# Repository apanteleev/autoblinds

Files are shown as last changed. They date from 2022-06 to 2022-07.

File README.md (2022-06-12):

# AutoBlinds

This repository contains various project files necessary to build a smart home connected device that moves a roller shade up and down by its bead string. The automation part is based on an ESP8266 microcontroller that talks to an automation hub via Wi-Fi and MQTT and is fully compatible with Home Assistant. The mechanical part is based on a NEMA 17 stepper motor with a TMC2208 driver, and the case and gears are 3D printed. Using a 48mm 2A stepper motor is sufficient to move a heavy 2.6 x 2.4 meter roller blind up or down in 20 seconds.

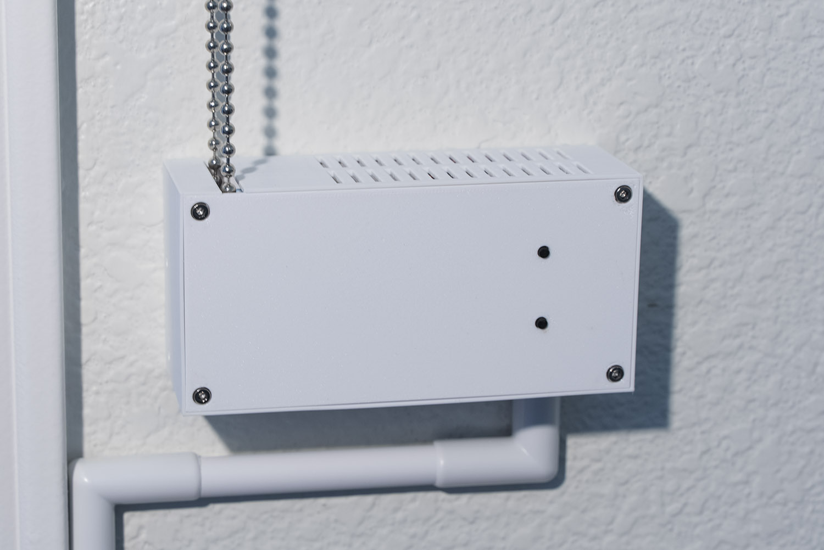
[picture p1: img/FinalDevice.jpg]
Final Device Image


## Origin

The project is inspired by another similar project, [ESPBlinds by se1exin](https://github.com/se1exin/ESPBlinds). The only parts reused from that project are the small gear and chain gears, everything else is rebuilt from scratch.

The main improvements are:

- Local control with up and down buttons
- Shade movement limits programmable from the buttons
- Soft start and stop
- Revised MQTT interface that is easily compatible with Home Assistant and supports moving the shade to a specific position
- Much smaller device by using a smaller big gear and packing things tighter in the case
- Quieter operation with the TMC2208 silent stepper driver

## Software

The software for the ESP8266 module is included here, see the [`autoblinds.ino`](autoblinds.ino) file. It builds with Arduino IDE version 1.8.19.

Additional steps before building:

- Install the ESP8266 boards for Arduino, see [this manual](https://arduino-esp8266.readthedocs.io/en/latest/installing.html)
- Install the PubSubClient library through the Arduino Library Manager.
- Copy the [`constants.example.h`](constants.example.h) file into `constants.h` and adjust the settings to match your network setup.

Build the project and program the board, it *should* work and report a connection to WiFi and MQTT through the serial port.

## Device Overview

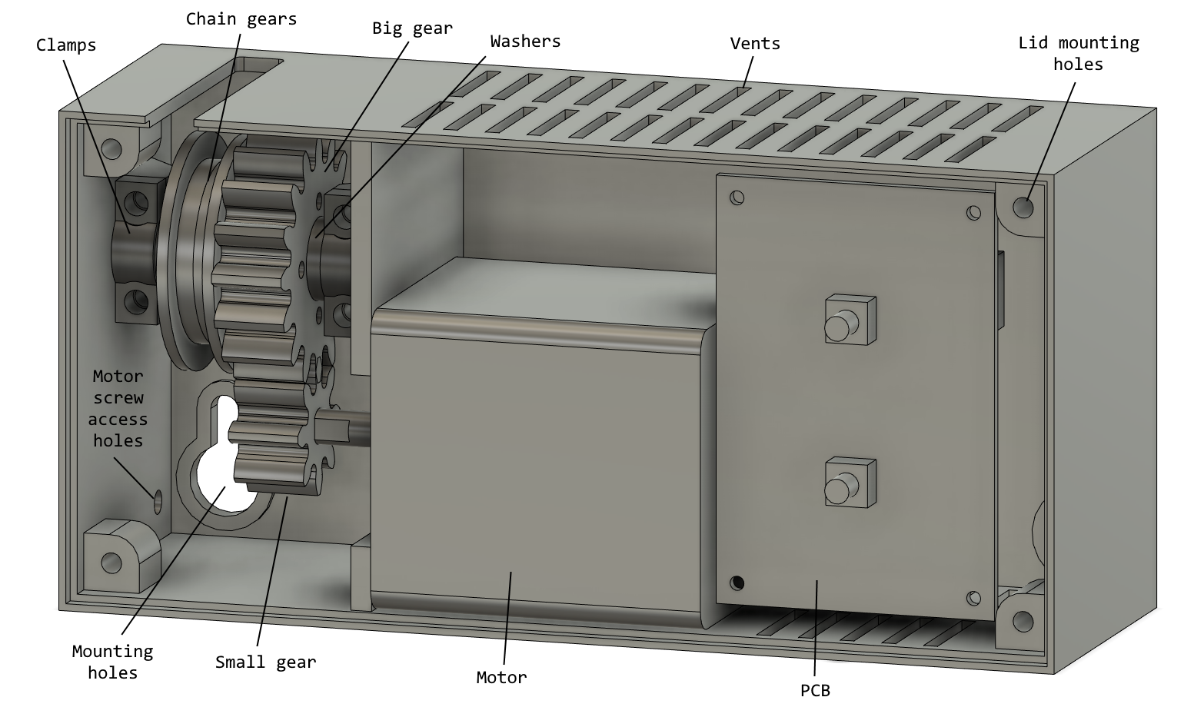
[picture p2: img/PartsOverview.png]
Parts Overview


## Button Operation

- Press the Up button to open the shade up to the top limit.
- Press the Down button to close the shade down to the bottom limit.
- While the shade is moving, press any button to stop it.
- Hold the Up button and press the Down button to set the top limit.
- Hold the Down button and press the Up button to set the bottom limit.
- Hold the Up or Down button for more than 0.5 seconds to open or close the shade beyond the limits (useful for setting the limits).

Note that while the limits are not set, the shade will not stop automatically. After assembling the device and uploading the program, make sure to set the limits first.

## Schematic Diagram

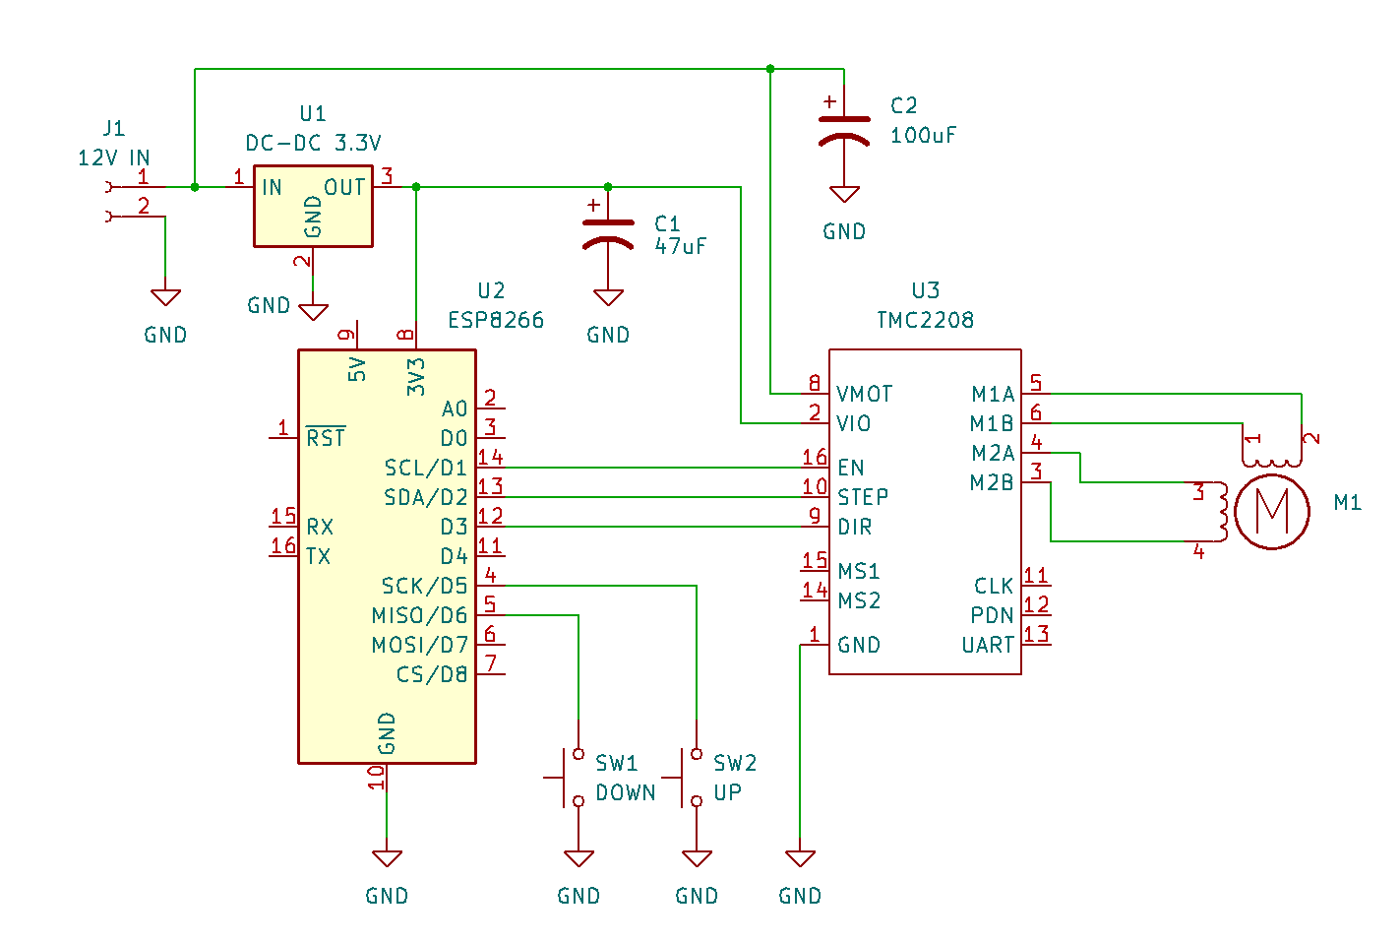
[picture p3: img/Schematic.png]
Schematic Diagram


## Parts

You'll need the following parts:

- 3D printed case and gears, including 2x ChainGear model. Use PETG filament for best results, not PLA. The models are available in the [models](models) folder in STL and as a Fusion 360 project.
- [ESP8266 board](https://www.amazon.com/dp/B081PX9YFV)
- [DC-DC converter](https://www.amazon.com/dp/B01MQGMOKI) capable of turning your input voltage into 3.3V for the ESP
- [TMC2208 stepper driver](https://www.amazon.com/dp/B08XV1HKYF)
- [NEMA 17 stepper motor](https://www.amazon.com/dp/B00PNEQKC0)
- 12-24V 2A+ power supply
- [4x6cm prototype PCB](https://www.amazon.com/dp/B07NM68FXK) and some header connectors
- [Push button switches](https://www.amazon.com/dp/B01MRP025V) - 2pc 6x6x8 mm
- Screws with hex caps: 12pc M3x8, 4pc M3x16, 4pc M2x6 - I used [this set](https://www.amazon.com/dp/B08JCKH31Q)
- Screws or anchors to mount the device to the wall - the selection depends on the wall material.
- Generic capacitors, wires, etc.
- Some grease and a Dremel with small drill bits

## Finished PCB

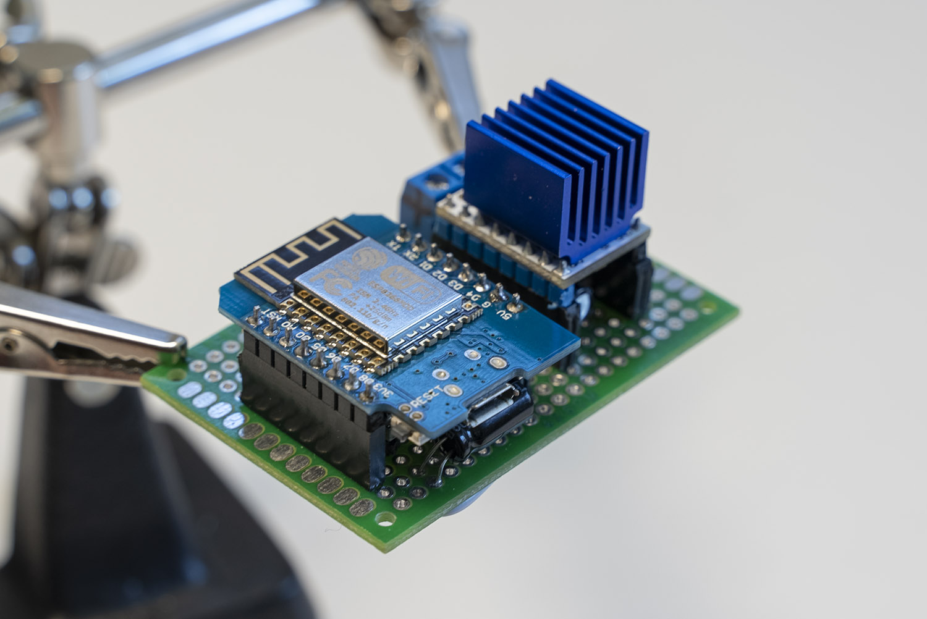
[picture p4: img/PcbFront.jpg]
Board Front Side


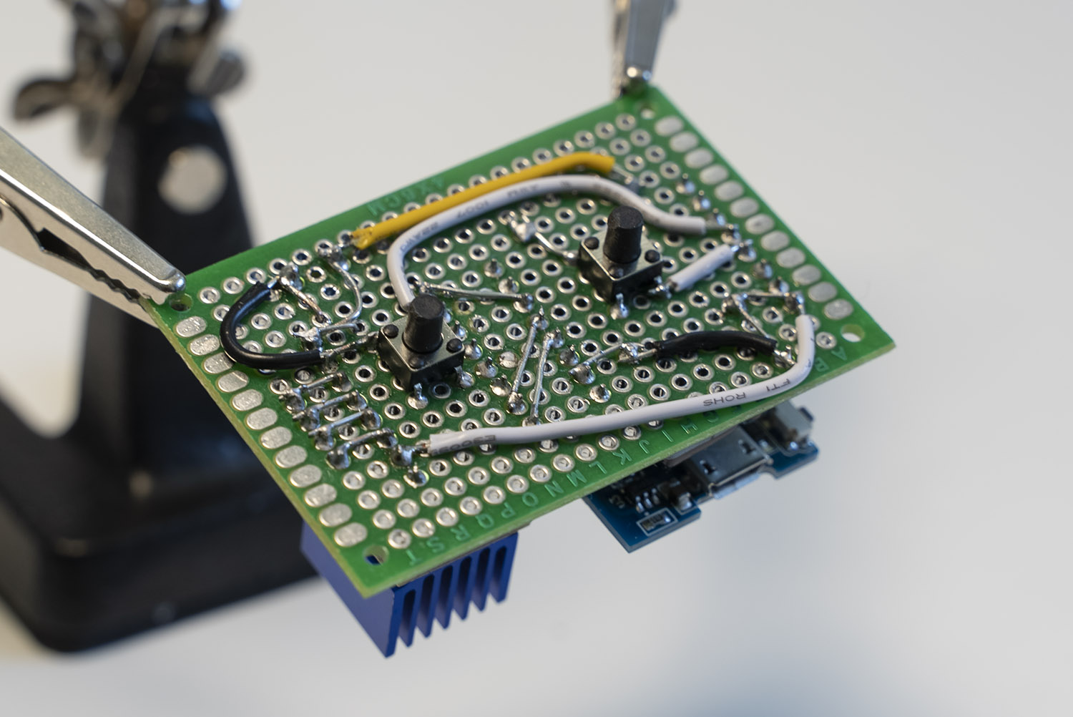
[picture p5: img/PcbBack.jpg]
Board Back Side


## Assembly steps

- Print the mechanical parts. None of them need any supports. The axle should be printed vertically with a brim, using as many perimeters as necessary to fill the entire volume.
- Drill the screw holes in the lid for the 4 M3 screws to pass freely.
- Put the small gear onto the motor axle. The fit should be very snug.
- Attach the motor to the case with 4 M3x8 screws. The two screws in the back can be accessed by putting an Allen key through the special holes on the left of the case.
- Connect the chain gears with the big gear using 4 M3x16 screws. The screws won't go easily through the holes in the chain gears, so just drill the holes a bit wider. I didn't design those chain gears so can't easily fix the models.
- Attach the PCB to the lid using 4 M2x6 screws.
- Put the big gear assembly onto the axle, add the washers - the wide one on the left, the narrow one on the right. The wide washer will need a little bit of Dremeling to fit between the screw heads.
- Make sure that the gear assembly and the axle fit into the case and things rotate freely. There might be some more Dremeling necessary to make things fit with little friction.
- Put the bead string through the chain gears.
- Insert the gear assembly into the case, secure the axle with the two clamps and tighten them with 4 M3x8 screws.
- Hold the device against the wall to figure out the right position to tension the string.
- Mount the device to the wall. Note that the mounting holes have vertical slots to adjust the tension. *In case you're wondering why the mounting holes are at the bottom, that's because when the device starts pulling on the string, this way it will just push the top side into the wall.*
- Connect the motor to the PCB, power it up and test.
- Adjust the current limiter on the stepper driver to make sure the current is enough to raise the shade without stalling. You may also want to adjust the speed parameters in the program, look for `MOTOR_MIN_SPEED`, `MOTOR_MAX_SPEED` and `MOTOR_ACCELERATION` in [`autoblinds.ino`](autoblinds.ino). Note that those steps are actually microsteps, and the default microstep for TMC2208 is 1/8 step when both MS1 and MS2 pins are low.
- Apply some grease on the gears and axle. This will likely require removing the gear assembly from the case, but doing it earlier would just be messy.
- Close the lid with 4 M3x8 screws. The lid may stick out in the middle; if that's the case, just put it on the 3D printer heatbed, heat that to the print temperature, and bend the lid a few degrees inwards. After cooling down, the lid will act like a spring.

## More Pictures

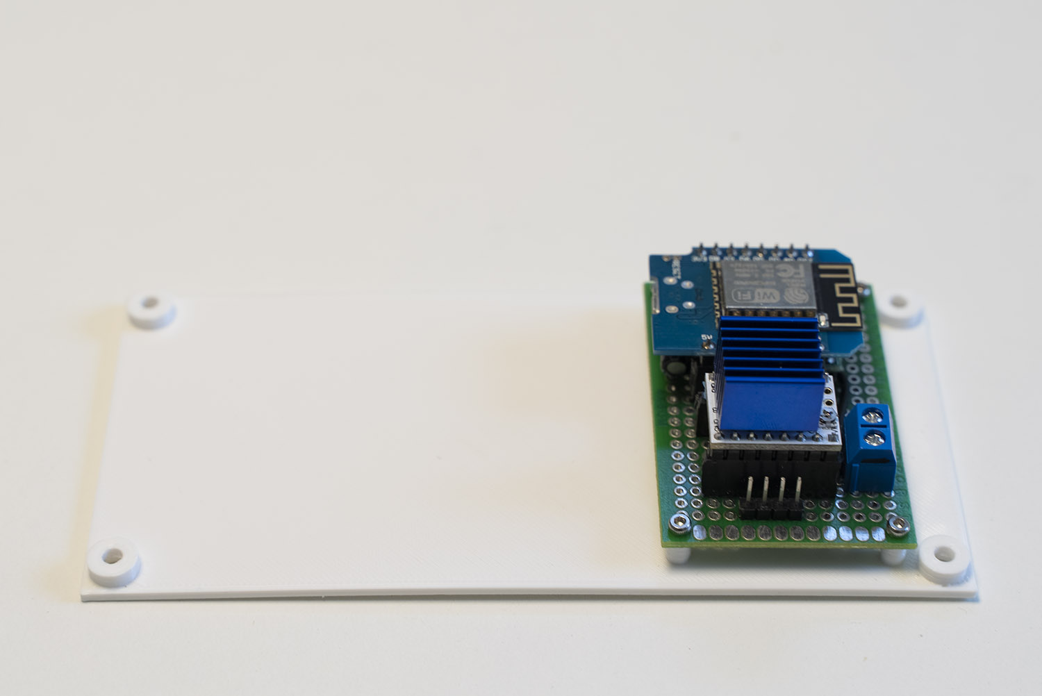
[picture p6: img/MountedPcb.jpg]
PCB Mounted on the Lid


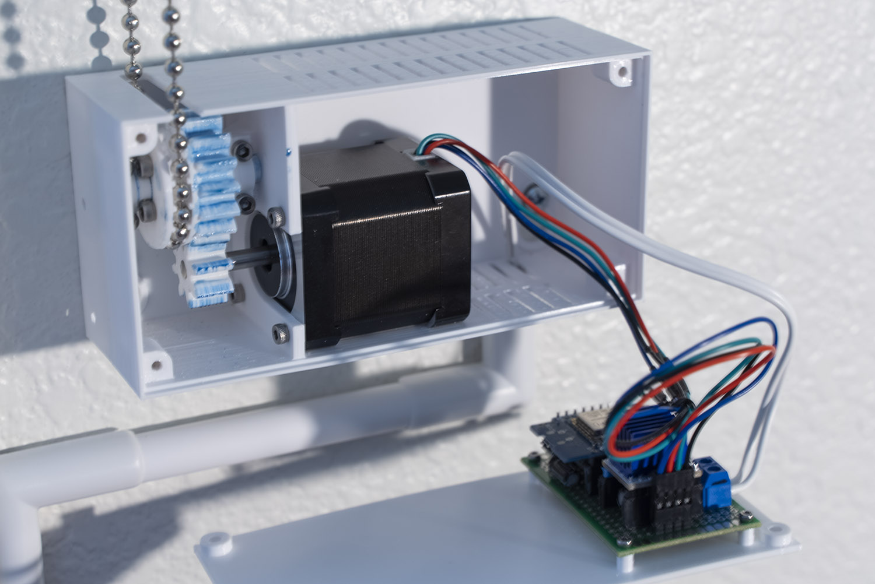
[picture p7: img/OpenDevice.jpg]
Assembled Device without Lid


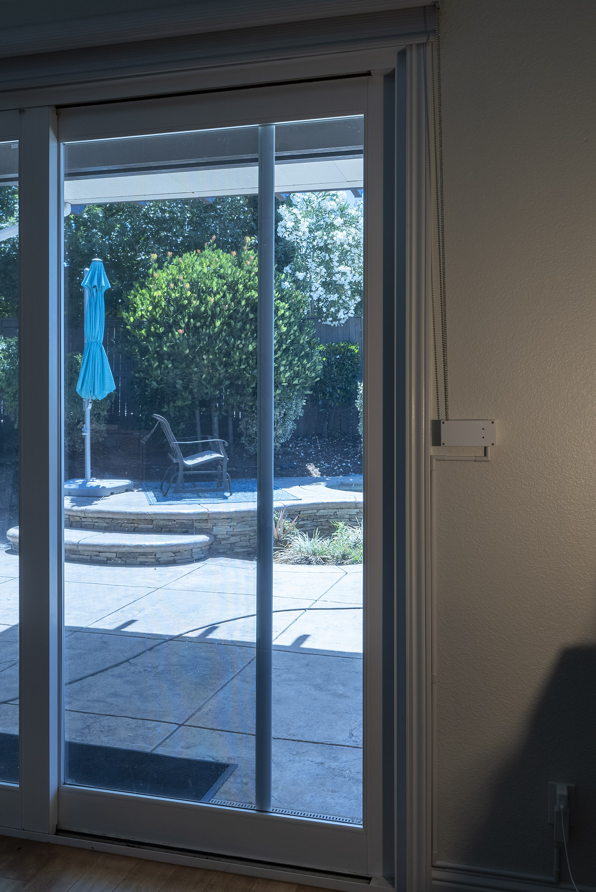
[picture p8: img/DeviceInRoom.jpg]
Device In The Room


## Home Assistant Integration

Home Assistant supports [MQTT shades](https://www.home-assistant.io/integrations/cover.mqtt) ("covers") natively, so you'll need to add something like this to `configuration.yaml`:

```yaml
mqtt:
  cover:
  - name: "Friendly Name"
    availability:
      # Note that the topic root used here 5 times (home/blinds/)
      # must match MQTT_TOPIC_ROOT defined in constants.h
      - topic: "home/blinds/status"
    command_topic: "home/blinds/command"
    payload_open: "open"
    payload_close: "close"
    payload_stop: "stop"
    position_topic: "home/blinds/position"
    set_position_topic: "home/blinds/setposition"
    state_topic: "home/blinds/state"
```

Obviously, you'll also need an [MQTT broker](https://mosquitto.org), but that's very easy to set up.

## What Could Be Improved

- Limit switches would solve the issue of position drift: when the motor disengages, the gears move a bit releasing the string tension. That movement is not registered by the controller. Also, if someone moves the shade manually, the limits currently need to be reset because manual motion is also not registered by the MCU.
- There's no user-friendly way of setting up the Wi-Fi and MQTT parameters. Other devices host an access point that is used for such initial setup.
- The orientation of the driver module makes the radiator fins horizontal, while vertical orientation is better. Originally I used the DRV8825 driver, and its radiator could be attached the other way.
- The orientation of the ESP module on my PCB prevents attaching a USB cable without removing the board from the device.
- No barrel connector for power, although it's not much of a problem as the cable just goes through one of the vent slots and into the cord cover.
- Tiny round buttons sticking out don't look so well, and it's possible to make button caps with e.g. triangular shape pointing up and down. The buttons should probably be shorter in that case, and the lid holes should match the button shape.
- Using a real custom PCB would just look better.

## Feedback

If you have any suggestions or comments, feel free to post issues or pull requests here on GitHub. Constructive criticism is welcome, especially considering that I'm relatively new to this type of engineering.

## License

This project is distributed under the terms of the [MIT License](LICENSE.txt).

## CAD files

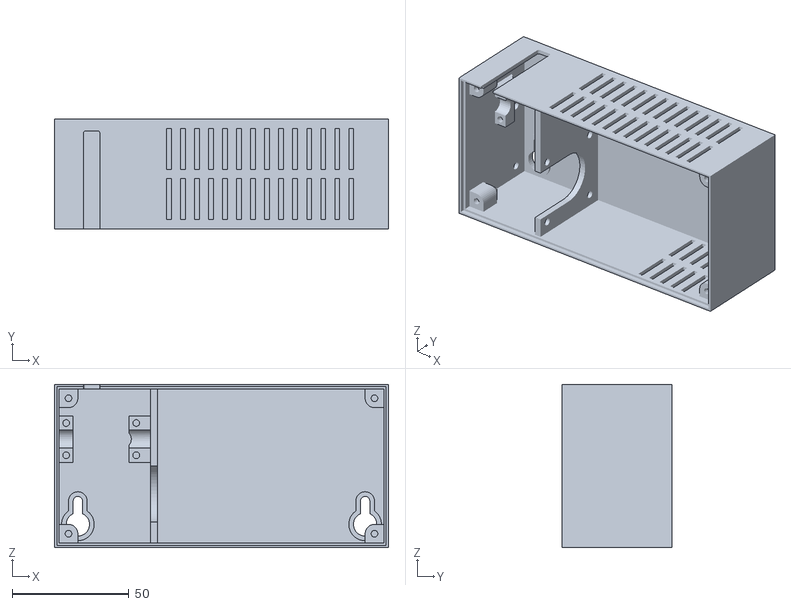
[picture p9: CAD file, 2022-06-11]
models/Case.stl
143.0 x 47.0 x 70.0

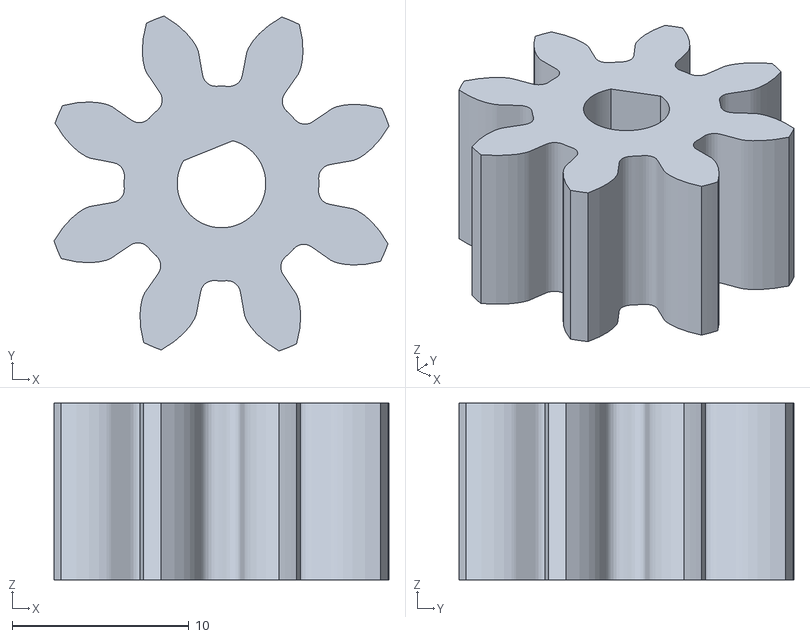
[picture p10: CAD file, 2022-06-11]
models/SmallGear.stl
18.9 x 18.9 x 10.0

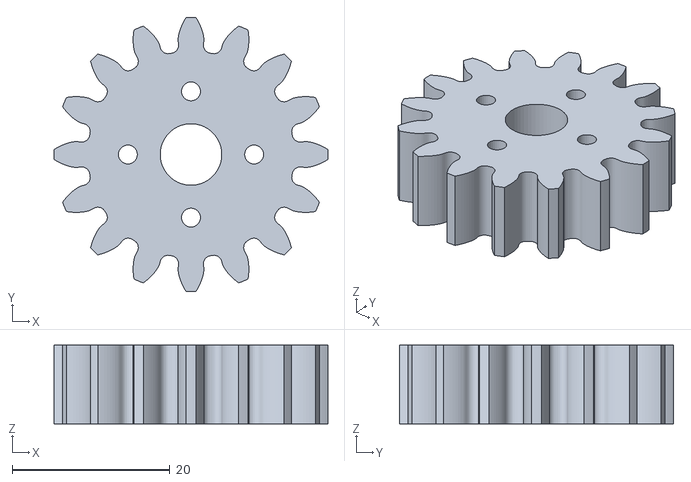
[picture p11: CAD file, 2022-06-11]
models/BigGear.stl
34.7 x 34.7 x 10.0

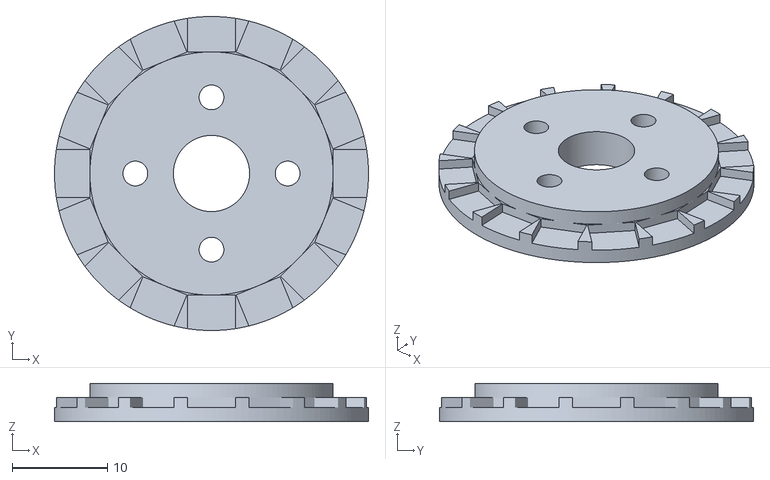
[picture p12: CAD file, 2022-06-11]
models/ChainGears.stl
33.0 x 33.0 x 4.00

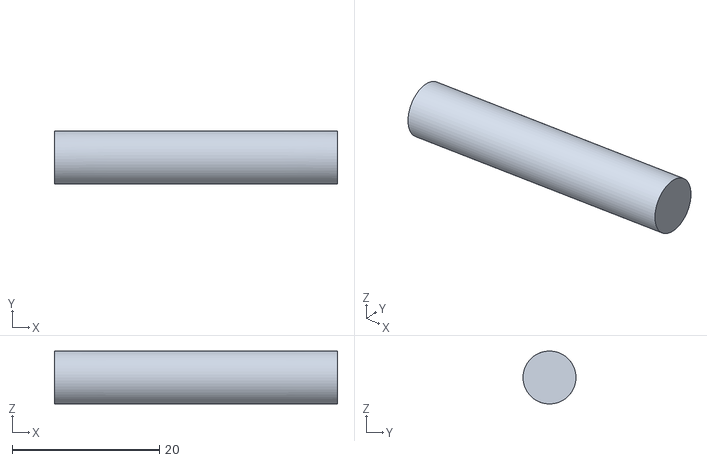
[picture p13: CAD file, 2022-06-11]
models/Axle.stl
38.5 x 7.20 x 7.20

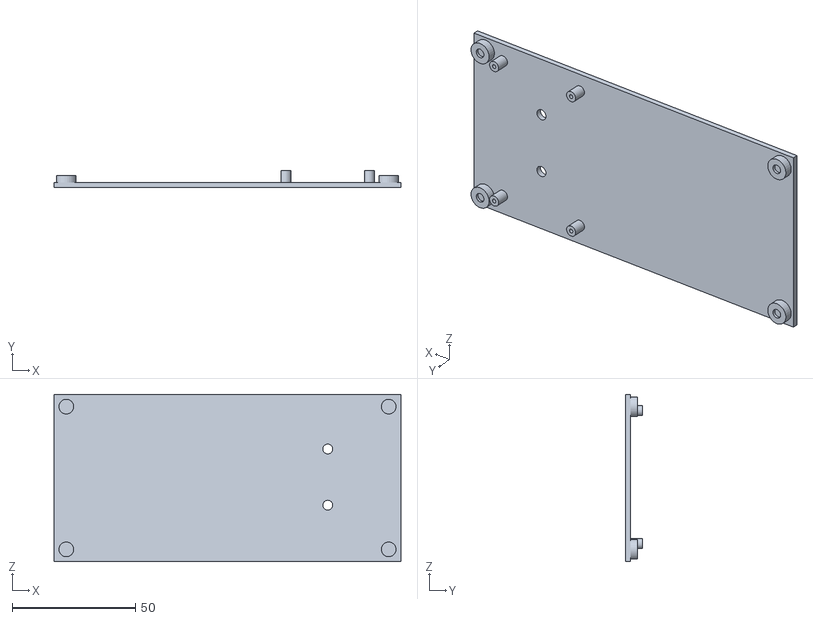
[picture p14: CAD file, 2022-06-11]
models/Lid.stl
141.0 x 7.00 x 68.0

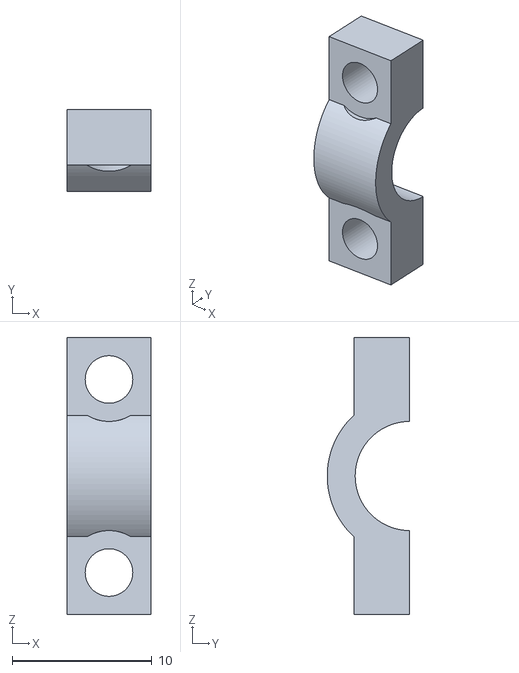
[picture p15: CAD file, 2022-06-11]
models/AxleClamp.stl
6.00 x 5.90 x 19.8

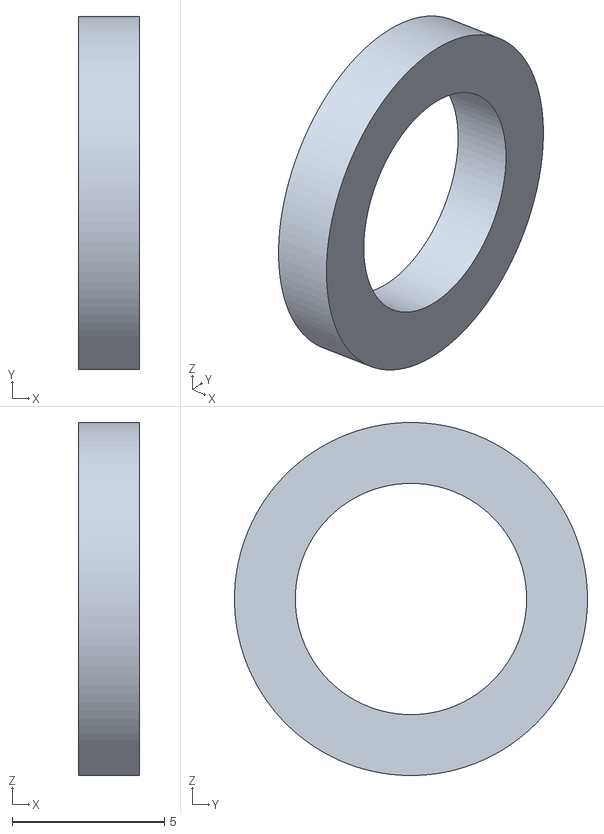
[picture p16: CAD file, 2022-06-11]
models/Washer2.stl
2.00 x 11.6 x 11.6

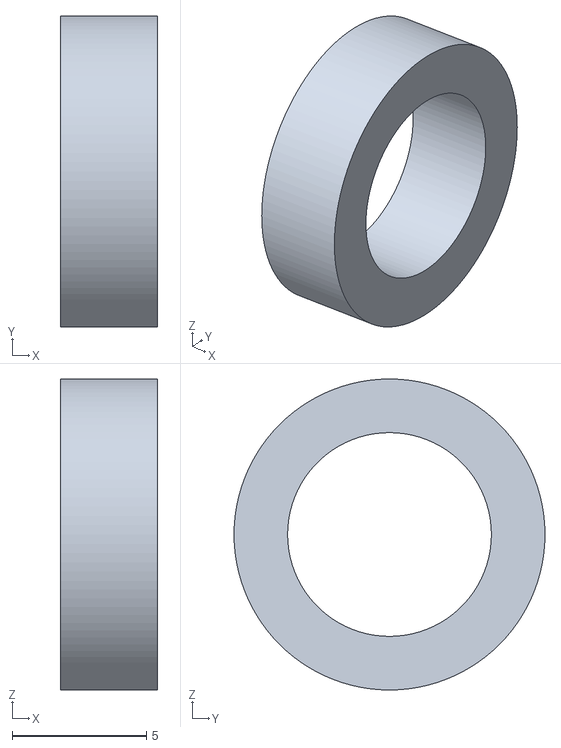
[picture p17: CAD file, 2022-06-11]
models/Washer1.stl
3.60 x 11.6 x 11.6

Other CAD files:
models/AutoBlinds.f3d

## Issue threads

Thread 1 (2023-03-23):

Position drift solution

friendlyFriend4000, 2023-03-23:
`Limit switches would solve the issue of position drift: when the motor disengages, the gears move a bit releasing the string tension. That movement is not registered by the controller. Also, if someone moves the shade manually, the limits currently need to be reset because manual motion is also not registered by the MCU.`

may I suggest another approach to solve the problem of position drift. Worm gears have the feature of "locking" when the motor is turned off. The downside is that the blinds will move slower, though.

apanteleev, 2023-03-23:
Thanks for the suggestion, but your solution also has issues. The most important one is that I think it's important to be able to move the shade manually, for example in case of a power outage. Also, worm gears have much higher friction than bevel gears, which will probably make the 3d printed gears wear quicker - although I admit I have no experience with such gears.

Based on using this shade controller for almost a year, I can say that position drift is not a big issue. I didn't have to adjust the limits in months.

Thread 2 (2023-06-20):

IR remote control

vulubalulu, 2023-06-20:
i came over from se1exin and discovered your version of the automatic blind system. I love it and I have build it successfully myself. Originally I used a4988 stepper driver but they were loud as hell and tmc have much much quieter drivers.
I put the blinds in my grandmothers apartment because she is too weak to open them herself at this point. Unfortunately she is also too old to operate them through a web browser. I bought a cheap IR remote and a 3 pin IR receiver in the hope that this will bet he final solution. I also thought I would be smart enough to modify your code to implement IR control but that's not the case. I really need your guidance.
My idea was to insert the IR code signal alongside the button commands of up and down, but I am simply lost. ANy help would be appreciated.

apanteleev, 2023-06-26:
Thanks for your feedback!

For IR control, I would add a separate IR handler function or class, call it from the main loop, and do something like this inside:

```
if (IrReceiver.decode()) {
  IrReceiver.resume();
  switch(IrReceiver.decodedIRData.command) {
    case IR_COMMAND_UP: // define the constant to your preferred remote button
        if (motor.isRunning())
          motor.softStop();
        else
          motor.start(MOTOR_DIRECTION_UP, false);
    case IR_COMMAND_DOWN: // etc...
  }
}
```

friendlyFriend4000, 2023-07-02:
Hello Alexey and thank you for getting back to me.
Your hint and code snippet helped me immensely. After many hours deep into the night I finally have a working remote control! I did spend almost all of my time troubleshooting. At first I could not get the motor to spin at all, the buttons wouldn't work either no matter what I did. Just 'IRremote.begin(PIN)' was enough for the microcontroller to freeze up. The solution was to use the library IRremoteESP8266 which magically worked off the bat if not for the random crashes. I found a exception decoder which pointed at motor.processTimer() in the onTimerInterrupt() function. This one really stumped me and I was at my wits end as googling wasn't helping either. Turns that having following the library example code and putting delays into the loop function was causing these exceptions, live and learn.
Anyway, it is working and I am beyond happy. I want to thank you once again for helping me out and for creating such a great program. My grandmother sends her regards as well.

apanteleev, 2023-07-03:
Cool, glad you got it all working!

The conflict of motor interrupt and IR receiver makes sense, I guess the IR libraries might use the same interrupt or other similar things.

If you can post a picture of your completed device, that would be great. :)

friendlyFriend4000, 2023-07-16:
You may use the images in any way you like.

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

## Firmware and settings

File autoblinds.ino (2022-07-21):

/*
Copyright (C) 2022, Alexey Panteleev.

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
THE SOFTWARE IS PROVIDED "AS IS", WITHOUT WARRANTY OF ANY KIND, EXPRESS OR
IMPLIED, INCLUDING BUT NOT LIMITED TO THE WARRANTIES OF MERCHANTABILITY,
FITNESS FOR A PARTICULAR PURPOSE AND NONINFRINGEMENT. IN NO EVENT SHALL THE
AUTHORS OR COPYRIGHT HOLDERS BE LIABLE FOR ANY CLAIM, DAMAGES OR OTHER
LIABILITY, WHETHER IN AN ACTION OF CONTRACT, TORT OR OTHERWISE, ARISING FROM,
OUT OF OR IN CONNECTION WITH THE SOFTWARE OR THE USE OR OTHER DEALINGS IN THE
SOFTWARE.
*/

#include <EEPROM.h>
#include <ESP8266WiFi.h>
#include <PubSubClient.h>

// Include the header that defines system-specific constants: WiFi network parameters and MQTT settings.
// The file is not included in git, so use 'constants.example.h' as a template.
#include "constants.h"


// Status - sends "online" or "offline" as last-will
#define MQTT_TOPIC_STATUS (MQTT_TOPIC_ROOT "status")
// Command - receives "open", "close"
#define MQTT_TOPIC_COMMAND (MQTT_TOPIC_ROOT "command")
// Status - sends "open", "closed", "opening", "closing", "stopped"
#define MQTT_TOPIC_STATE (MQTT_TOPIC_ROOT "state")
// Position - sends position percentage, 0..100
#define MQTT_TOPIC_POSITION (MQTT_TOPIC_ROOT "position")
// Set position - receives position percentage to set, 0..100
#define MQTT_TOPIC_SET_POSITION (MQTT_TOPIC_ROOT "setposition")

#define PIN_BUTTON_UP D5
#define PIN_BUTTON_DOWN D6
#define PIN_MOTOR_DIR D3
#define PIN_MOTOR_STEP D2
#define PIN_MOTOR_NEN D1
#define PIN_LED LED_BUILTIN

#define LED_INTERVAL 100 // milliseconds

// LED blinking patterns.
// Each bit represents an interval of LED_INTERVAL milliseconds, displayed right to left.
#define LED_START_STOP  0b1
#define LED_LIMIT       0b101
#define LED_SAVE        0b1110011
#define LED_STARTUP     0b1111

class LedPulser {
private:
  unsigned long lastUpdateTime = 0;
  unsigned int pattern = 0;

  void advance() {
    lastUpdateTime = millis();
    digitalWrite(PIN_LED, !(pattern & 1));
    pattern = pattern >> 1;
  }
  
public:
  void setup() {
    pinMode(PIN_LED, OUTPUT);
    advance();
  }

  void loop() {
    if (millis() >= lastUpdateTime + LED_INTERVAL) {
      advance();
    }
  }

  void show(unsigned int _pattern) {
    pattern = _pattern;
    advance();
  }
};

LedPulser led;


#define BUTTON_PRESSED 1
#define BUTTON_RELEASED -1
#define BUTTON_DEBOUNCE_DELAY 5 // milliseconds
#define BUTTON_HOLD_DURATION 500

class ButtonWithDebounce {
  // Based on the code from https://docs.arduino.cc/built-in-examples/digital/Debounce 
private:
  int buttonPin;
  bool pullup;
  
  int buttonState = LOW;
  int lastButtonState = LOW;
  int change = 0;
  unsigned long lastDebounceTime = 0;
  
public:
  ButtonWithDebounce(int pin, bool pullup)
    : buttonPin(pin)
    , pullup(pullup)
  {}

  void setup() {
    if (pullup)
      pinMode(buttonPin, INPUT_PULLUP);
    else
      pinMode(buttonPin, INPUT);
  }

  void read() {
    int reading = digitalRead(buttonPin);
    if (pullup) {
        reading = !reading;
    }

    unsigned long currentTime = millis();
    
    if (reading != lastButtonState) {
      lastDebounceTime = currentTime;
    }
  
    if (reading != buttonState && (currentTime - lastDebounceTime) > BUTTON_DEBOUNCE_DELAY) {
      change = reading - buttonState;
      buttonState = reading;
    }
    else {
      change = 0;
    }
  
    lastButtonState = reading;
  }

  int getState() { return buttonState; } // returns LOW or HIGH, after pullup correction
  int getChange() { return change; } // returns BUTTON_PRESSED or BUTTON_RELEASED

  bool pressed() { return change == BUTTON_PRESSED; }
  bool released() { return change == BUTTON_RELEASED; }
};

ButtonWithDebounce buttonUp(PIN_BUTTON_UP, true);
ButtonWithDebounce buttonDown(PIN_BUTTON_DOWN, true);


#define EEPROM_MAGIC 0x5A0D3C67 // a random number

// A struct that is directly mapped to the simulated "EEPROM".
// On ESP8266, the EEPROM is just a block of flash memory that is read into a RAM segment and written at once.
struct Settings {
  unsigned long magic;
  long position;
  long positionTop;
  long positionBottom;
  
  static Settings* load() { 
    // Read the existing data from flash
    EEPROM.begin(sizeof(Settings));

    // Cast that data to our structure
    Settings* data = (Settings*)EEPROM.getDataPtr();

    // If the data is not valid, initialize with some values and write
    if (data->magic != EEPROM_MAGIC) {
      data->magic = EEPROM_MAGIC;
      data->position = 0;
      data->positionTop = 0;
      data->positionBottom = 0;
      EEPROM.commit();
    }

    return data;
  }

  void save() {
    EEPROM.getDataPtr(); // mark the data as dirty
    EEPROM.commit();
  }

  // Tells if the current position is above the top limit (minus margin) or under the bottom limit (plus margin)
  // Also supports a targetPosition parameter that can be received via a MQTT command
  bool isOffLimits(bool up, long margin, long targetPosition) {
    if (up && positionTop != 0 && position + margin >= positionTop)
      return true;
    if (!up && positionBottom != 0 && position - margin <= positionBottom)
      return true;
      
    if (targetPosition != 0) {
      if (up && position + margin >= targetPosition)
        return true;
      if (!up && position - margin <= targetPosition)
        return true;
    }
    
    return false;
  }

  // Saves the current position as either the top or the bottom one
  void saveLimit(bool up) {
    if (up)
      positionTop = (position == 0) ? 1L : position;
    else
      positionBottom = (position == 0) ? -1L : position;

    save();
  }
};

// Motor controller FSM states
#define MSTATE_IDLE 0
#define MSTATE_ACCELERATE 1
#define MSTATE_RUN 2
#define MSTATE_DECELERATE 3
#define MSTATE_BACKSPIN 4

#define MOTOR_MIN_SPEED 200     // steps per second
#define MOTOR_MAX_SPEED 3000    // steps per second
#define MOTOR_ACCELERATION 4000 // steps per sedond per second

// Number of steps to take in the opposite direction after decelerating and before disconnecting the motor, to release tension
#define MOTOR_BACKSPIN_STEPS 800
#define MOTOR_BACKSPIN_SPEED 800

// Solution for the distance of an accelerated object traveling between two speed values
#define MOTOR_ACCELERATION_STEPS ((MOTOR_MAX_SPEED * MOTOR_MAX_SPEED - MOTOR_MIN_SPEED * MOTOR_MIN_SPEED) / (2 * MOTOR_ACCELERATION))

#define MICROSECONDS_IN_SECOND 1000000L

// DIR pin values that correspond to up or down directions
#define MOTOR_DIRECTION_UP HIGH
#define MOTOR_DIRECTION_DOWN LOW

// ESP8266 hardware timer settings
#define TIMER_DIVIDER TIM_DIV16
#define TIMER_TICKS_PER_SECOND 5000000

// Forward declarations for global functions that are used in MotorDriver but also use the driver object itself
void onTimerInterrupt();
void sendMqttState();

class MotorDriver {
private:
  int state = MSTATE_IDLE;
  long speed = 0; // in steps per second
  unsigned long accelerateStartMicros = 0;
  int direction = 0;
  int backspinStepsLeft = 0;
  bool ignoreLimits = false;
  long targetPosition = 0;
  Settings* settings = NULL;

  // Performs a full stop - for internal MotorDriver use only, use softStop() from user side instead
  void stop() {
    speed = 0;
    state = MSTATE_IDLE;
    targetPosition = 0;
    digitalWrite(PIN_MOTOR_NEN, HIGH);
    digitalWrite(PIN_MOTOR_STEP, LOW);
    
    timer1_disable();

    // Save the position in non-volatile memory in case there is a power loss
    settings->save();

    sendMqttState();
  }

  // Sets the timer to wake up when it's time to do the next step.
  // The interval is adjusted by elapsedMicroseconds to account for the time spent in processTimer before calling this function.
  void scheduleStep(uint32_t elapsedMicroseconds = 0) {
    if (speed == 0)
      return;
      
    uint32_t stepInterval = TIMER_TICKS_PER_SECOND / speed;
    uint32_t elapsedTicks = elapsedMicroseconds * (TIMER_TICKS_PER_SECOND / MICROSECONDS_IN_SECOND);
    if (stepInterval > elapsedTicks)
      stepInterval -= elapsedTicks;
    else
      stepInterval = 1;

    // Wake up once after 'stepInterval' timer ticks
    timer1_enable(TIMER_DIVIDER, TIM_EDGE, TIM_SINGLE);
    timer1_write(stepInterval);
  }

public:
  void setup(Settings* _settings) {
    settings = _settings;
  
    pinMode(PIN_MOTOR_DIR, OUTPUT);
    pinMode(PIN_MOTOR_STEP, OUTPUT);
    pinMode(PIN_MOTOR_NEN, OUTPUT);
    digitalWrite(PIN_MOTOR_DIR, LOW);
    digitalWrite(PIN_MOTOR_STEP, LOW);
    digitalWrite(PIN_MOTOR_NEN, HIGH);

    timer1_attachInterrupt(onTimerInterrupt);
  }

  void processTimer() {
    if (state == MSTATE_IDLE)
      return;
      
    unsigned long entranceMicros = micros();

    // Pulse the step pin
    digitalWrite(PIN_MOTOR_STEP, HIGH);
    delayMicroseconds(20);
    digitalWrite(PIN_MOTOR_STEP, LOW);
    
    // Update the position
    if (direction == MOTOR_DIRECTION_UP)
      ++settings->position;
    else
      --settings->position;

    // Adjust the speed if we're accelerating or decelerating
    switch(state) {
    case MSTATE_ACCELERATE:
      speed = MOTOR_MIN_SPEED + ((entranceMicros - accelerateStartMicros) * MOTOR_ACCELERATION) / MICROSECONDS_IN_SECOND;
      if (speed >= MOTOR_MAX_SPEED) {
        speed = MOTOR_MAX_SPEED;
        state = MSTATE_RUN;
      }
      break;
    case MSTATE_DECELERATE:
      speed = MOTOR_MAX_SPEED - ((entranceMicros - accelerateStartMicros) * MOTOR_ACCELERATION) / MICROSECONDS_IN_SECOND;
      if (speed <= MOTOR_MIN_SPEED) {
        backspinStepsLeft = MOTOR_BACKSPIN_STEPS;
        state = MSTATE_BACKSPIN;
        direction = !direction;
        digitalWrite(PIN_MOTOR_DIR, direction);
      }
      break;
    case MSTATE_BACKSPIN:
      speed = MOTOR_BACKSPIN_SPEED;
      if (--backspinStepsLeft <= 0)
        stop();
      break;
    }

    if (!ignoreLimits && state != MSTATE_BACKSPIN) {
      // Stop at the limits, if they are set
      if (settings->isOffLimits(direction == MOTOR_DIRECTION_UP, MOTOR_ACCELERATION_STEPS, targetPosition))
        softStop();
    }

    // Set the timer for the next step pulse
    unsigned long exitMicros = micros();
    scheduleStep(exitMicros - entranceMicros);
  }

  void start(int _direction, bool _ignoreLimits) {
    if (state != MSTATE_IDLE)
      return;
      
    direction = _direction;
    ignoreLimits = _ignoreLimits;

    if (!ignoreLimits) {
      // Don't start if we're off limits
      if (settings->isOffLimits(direction == MOTOR_DIRECTION_UP, MOTOR_ACCELERATION_STEPS, targetPosition)) {
        led.show(LED_LIMIT);
        return;
      }
    }

    // Start up the driver
    digitalWrite(PIN_MOTOR_NEN, LOW);
    digitalWrite(PIN_MOTOR_DIR, direction);
    digitalWrite(PIN_MOTOR_STEP, LOW);
    
    // Make sure that the enable and direction pins are held in the right state for at least 1us
    // before giving any step commands
    delayMicroseconds(1);
    
    state = MSTATE_ACCELERATE;
    speed = MOTOR_MIN_SPEED;

    // Initialize the accelerator
    accelerateStartMicros = micros();

    // Start the timer
    scheduleStep();
    
    led.show(LED_START_STOP);
    
    sendMqttState();
  }

  void softStop() {
    if (state == MSTATE_ACCELERATE || state == MSTATE_RUN) {
      state = MSTATE_DECELERATE;
      accelerateStartMicros = micros();
      
      led.show(LED_START_STOP);
    }
  }

  bool isRunning() {
    return state != MSTATE_IDLE;
  }

  void saveLimitPosition(int direction) {
    if (isRunning())
      return;

    led.show(LED_SAVE);
    
    settings->saveLimit(direction == MOTOR_DIRECTION_UP);
  }

  int getDirection() { return direction; }

  bool getPositionPercentage(int& percent) {
    long positionDiff = settings->positionTop - settings->positionBottom - MOTOR_BACKSPIN_STEPS * 2;
    if (settings->positionTop == 0 || settings->positionBottom == 0 || positionDiff <= 0)
      return false;

    percent = ((settings->position - settings->positionBottom - MOTOR_BACKSPIN_STEPS) * 100 + (positionDiff >> 1)) / positionDiff;
    percent = max(0, min(100, percent));
    return true;
  }

  void startTo(int percent) {
    if (isRunning())
      return;
      
    if (settings->positionTop == 0 || settings->positionBottom == 0 || settings->positionTop == settings->positionBottom)
      return;

    if (percent < 0 || percent > 100)
      return;

    targetPosition = settings->positionBottom + ((settings->positionTop - settings->positionBottom) * percent) / 100;
    if (targetPosition < settings->position) {
      if (targetPosition == 0) targetPosition = -1;
      start(MOTOR_DIRECTION_DOWN, false);
    }
    else if (targetPosition > settings->position) {
      if (targetPosition == 0) targetPosition = 1;
      start(MOTOR_DIRECTION_UP, false);
    }
  }
};

MotorDriver motor;

void onTimerInterrupt() {
  motor.processTimer();
}


#define INPUT_IDLE 0
#define INPUT_UP 1
#define INPUT_UP_FORCED 2
#define INPUT_DOWN 3
#define INPUT_DOWN_FORCED 4

class InputHandler {
private:
  int inputState = INPUT_IDLE;
  unsigned long pressTime = 0;

public:
  void setup() {
    buttonUp.setup();
    buttonDown.setup();
  }
  
  void loop() {
    buttonUp.read();
    buttonDown.read();

    // Process the button states and decide what to do:
    // - Up or down button pressed briefly: start moving up or down when the button is released, or stop if already moving
    // - Up or down button held for more than 0.5 seconds: move up or down while the button is held, ignore the top and bottom limits
    // - Up button held, down button pressed: save the current position as the top limit
    // - Down button held, up button pressed: save the current position as the bottom limit
  
    switch(inputState) {
    case INPUT_IDLE:
      if (buttonUp.pressed()) {
        inputState = INPUT_UP;
        pressTime = millis();
      } else if (buttonDown.pressed()) {
        inputState = INPUT_DOWN;
        pressTime = millis();
      }
      break;
    case INPUT_UP:
      if (buttonUp.released()) {
        if (motor.isRunning())
          motor.softStop();
        else
          motor.start(MOTOR_DIRECTION_UP, false);
        inputState = INPUT_IDLE;
      }
      else if (buttonDown.pressed()) {
        motor.saveLimitPosition(MOTOR_DIRECTION_UP);
        inputState = INPUT_IDLE;
      }
      else if (!motor.isRunning() && millis() >= pressTime + BUTTON_HOLD_DURATION) {
        motor.start(MOTOR_DIRECTION_UP, true);
        inputState = INPUT_UP_FORCED;
      }
      break;
    case INPUT_UP_FORCED:
      if (buttonUp.released()) {
        motor.softStop();
        inputState = INPUT_IDLE;
      }
      break;
    case INPUT_DOWN:
      if (buttonDown.released()) {
        if (motor.isRunning())
          motor.softStop();
        else
          motor.start(MOTOR_DIRECTION_DOWN, false);
        inputState = INPUT_IDLE;
      }
      else if (buttonUp.pressed()) {
        motor.saveLimitPosition(MOTOR_DIRECTION_DOWN);
        inputState = INPUT_IDLE;
      }
      else if (!motor.isRunning() && millis() >= pressTime + BUTTON_HOLD_DURATION) {
        motor.start(MOTOR_DIRECTION_DOWN, true);
        inputState = INPUT_DOWN_FORCED;
      }
      break;
    case INPUT_DOWN_FORCED:
      if (buttonDown.released()) {
        motor.softStop();
        inputState = INPUT_IDLE;
      }
      break;
    }
  }
};

InputHandler input;

WiFiClient espClient;
PubSubClient mqttClient(espClient);

void mqttCallback(char* topic, byte* payload, unsigned int length) {
  String topicStr = topic;
  String value = "";
  for (int i = 0; i < length; i++) {
      value += (char)payload[i];
  }
  
  Serial.println("MQTT Received: ");
  Serial.println(topicStr);
  Serial.println(value);
  Serial.flush();

  if (topicStr == MQTT_TOPIC_COMMAND) {
    if (value == "open" && !motor.isRunning()) {
      motor.start(MOTOR_DIRECTION_UP, false);
    }
    else if (value == "close" && !motor.isRunning()) {
      motor.start(MOTOR_DIRECTION_DOWN, false);
    }
    else if (value == "stop" && motor.isRunning()) {
      motor.softStop();
    }
  }
  else if (topicStr == MQTT_TOPIC_SET_POSITION) {
    int position = value.toInt();
    motor.startTo(position);
  }
}

#define NSTATE_DISCONNECTED 0
#define NSTATE_WIFI_CONNECTING 1
#define NSTATE_MQTT_CONNECTING 2
#define NSTATE_MQTT_CONNECTED 3

class NetworkDriver {
private:
  int state = NSTATE_DISCONNECTED;
  unsigned long lastConnectTime = 0;
  
public:
  void loop() {
    switch(state) {
    case NSTATE_DISCONNECTED:
      WiFi.begin(WIFI_SSID, WIFI_PASSWORD);
      state = NSTATE_WIFI_CONNECTING;
      break;
    case NSTATE_WIFI_CONNECTING:
      if (WiFi.status() == WL_CONNECTED) {
        mqttClient.setServer(MQTT_BROKER, 1883);
        mqttClient.setCallback(mqttCallback);
        state = NSTATE_MQTT_CONNECTING;
        WiFi.printDiag(Serial);
        Serial.flush();
      }
      break;
    case NSTATE_MQTT_CONNECTING:
      if (WiFi.status() != WL_CONNECTED) {
        state = NSTATE_WIFI_CONNECTING;
      } else {
        unsigned long currentTime = millis();
        if (lastConnectTime == 0 || currentTime - lastConnectTime >= 10000) {
          if (mqttClient.connect(MQTT_CLIENT_ID, MQTT_USER, MQTT_PASSWORD, MQTT_TOPIC_STATUS, 0, true, "offline")) {
            lastConnectTime = 0;
            state = NSTATE_MQTT_CONNECTED;
            mqttClient.publish(MQTT_TOPIC_STATUS, "online", true);
            sendMqttState();
            mqttClient.subscribe(MQTT_TOPIC_COMMAND);
            mqttClient.subscribe(MQTT_TOPIC_SET_POSITION);
            Serial.println("Connected to MQTT.");
            Serial.flush();
          }
          else {
            lastConnectTime = currentTime;
          }
        }
      }
      break;
    case NSTATE_MQTT_CONNECTED:
      if (WiFi.status() != WL_CONNECTED) {
        state = NSTATE_WIFI_CONNECTING;
      } else {
        mqttClient.loop();
        if (!mqttClient.connected()) {
          state = NSTATE_MQTT_CONNECTING;
        }
      }
    }
  }

  bool connected() {
    return state = NSTATE_MQTT_CONNECTED;
  }
};

NetworkDriver network;

void sendMqttState() {
  if (!network.connected())
    return;

  String state;
  if (motor.isRunning()) {
    if (motor.getDirection() == MOTOR_DIRECTION_UP)
      state = "opening";
    else
      state = "closing";
  }
  else {
    int percentage;
    if (motor.getPositionPercentage(percentage)) {
      if (percentage == 0)
        state = "closed";
      else if (percentage == 100)
        state = "open";
      else
        state = "stopped";
      mqttClient.publish(MQTT_TOPIC_POSITION, String(percentage).c_str());
    }
    else
      state = "stopped";
  }

  mqttClient.publish(MQTT_TOPIC_STATE, state.c_str());
}


void setup() {
  Serial.begin(115200);
  Serial.println();
  Serial.println("Starting up...");
  Serial.flush();
  
  Settings* settings = Settings::load();
  
  led.setup();
  input.setup();
  motor.setup(settings);

  led.show(LED_STARTUP);
}

void loop() {
  input.loop();
  network.loop();
  led.loop();
  yield();
}

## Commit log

2022-06-11 Initial public commit.
    [AutoBlinds.f3d, Axle.stl, AxleClamp.stl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]
2022-06-12 Fixed a cut-and-paste bug in the Readme.
2022-07-21 Added backspin after decelerating to release tension.
2022-07-21 Fixed position calculation in the presence of backspin, adjusted max speed.
    [autoblinds.ino]
